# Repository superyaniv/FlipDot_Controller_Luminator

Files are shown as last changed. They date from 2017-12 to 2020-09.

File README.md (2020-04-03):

# FlipDot Controller Project

A FlipDot board was a unique way, before the cheap and ubiquitous LED displays, to display signage with low power and high visability. The unique innovation combines electrical engineering princples of electromagnetism, polarity, multiplexing, and much more. Not to mention it's just fun to see the complex mechanical switching in realtime. As I became interested in learning more about electrical engineering and design, this project, created in 2011 and posted on my public git recently, inspired me to begin learning circuit design. 

## Getting Started

The PCB schemetic uses 10 shift registers to drive darlington array source and pull down ICs. The pin layout is explained in the cvs file. From there, the project uses the flipdot controller python class to post bytes to the board and pin layout. The layer of abstraction above that can be a variance of code, depending on what to pull and post to the board. Examples included here are a clock, bitcoin price feed, and twitter display.

### Prerequisites

Hardware necessary to complete the code from scratch include:

```
10 x 595 Shift Registers
5 x ULN2803 Darlington Arrays
5 x Source Drivers (x2981)
Note: A different layout could use MOSFET transistors instead of these ICs.

1 x microcontroller (RPI or ESP8266 for use with this python code or Arduino )
```

### View of the PCB

Top, Bottom, and overall Design View of the PCB:

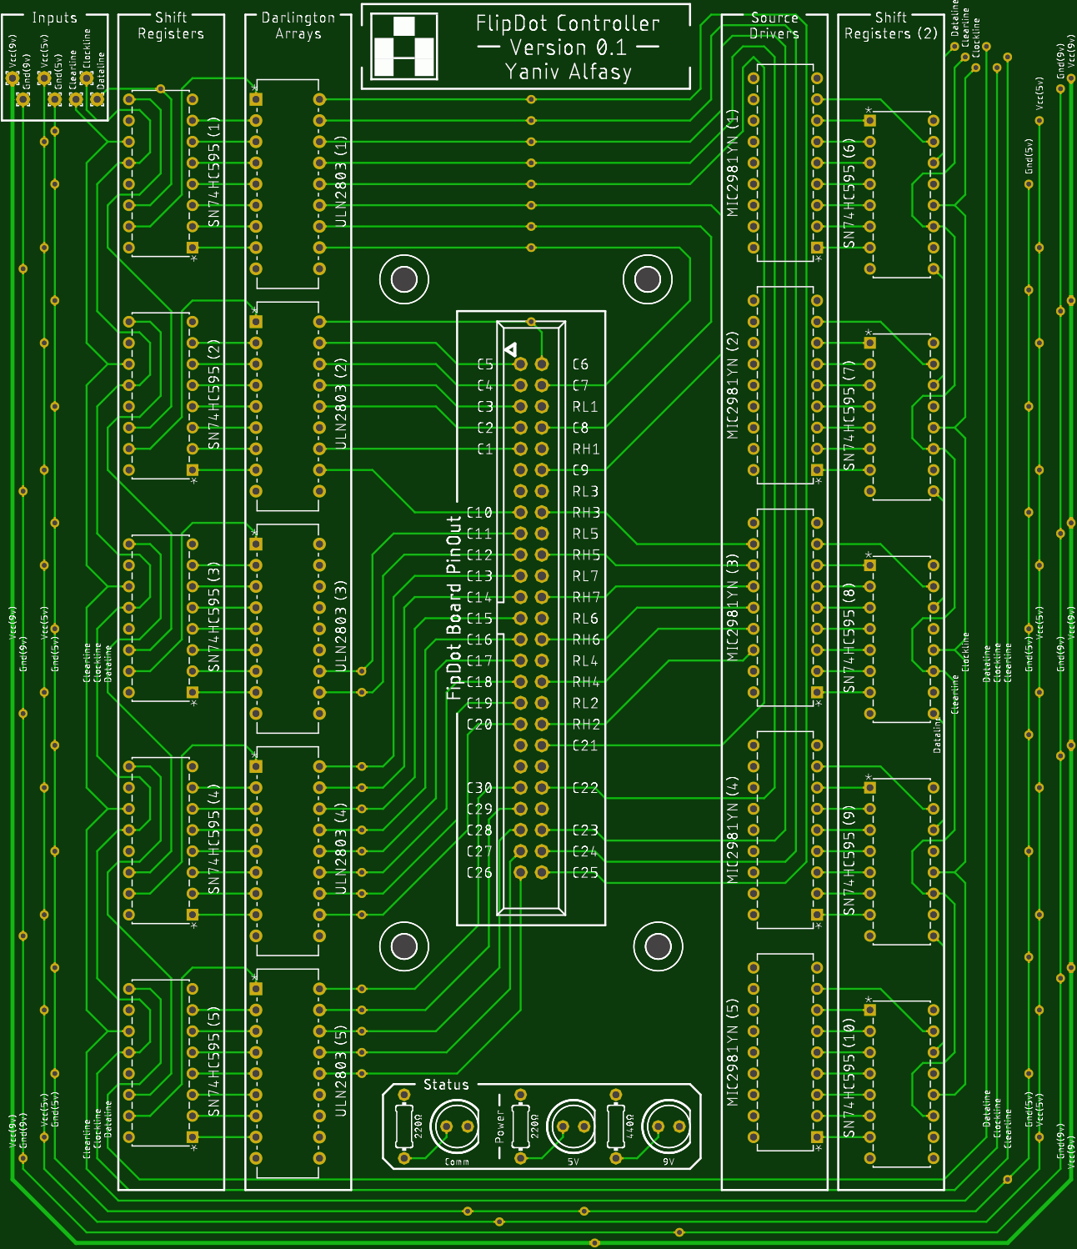
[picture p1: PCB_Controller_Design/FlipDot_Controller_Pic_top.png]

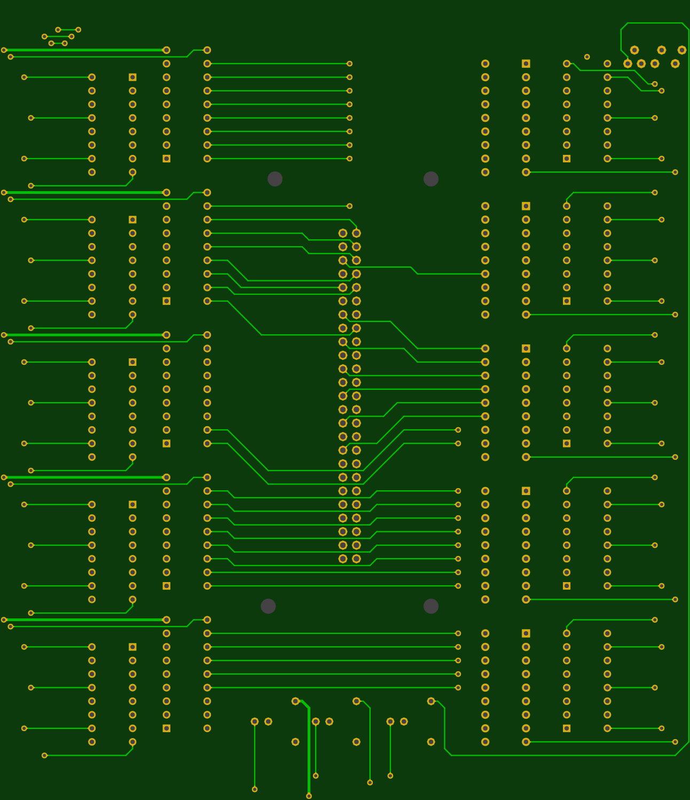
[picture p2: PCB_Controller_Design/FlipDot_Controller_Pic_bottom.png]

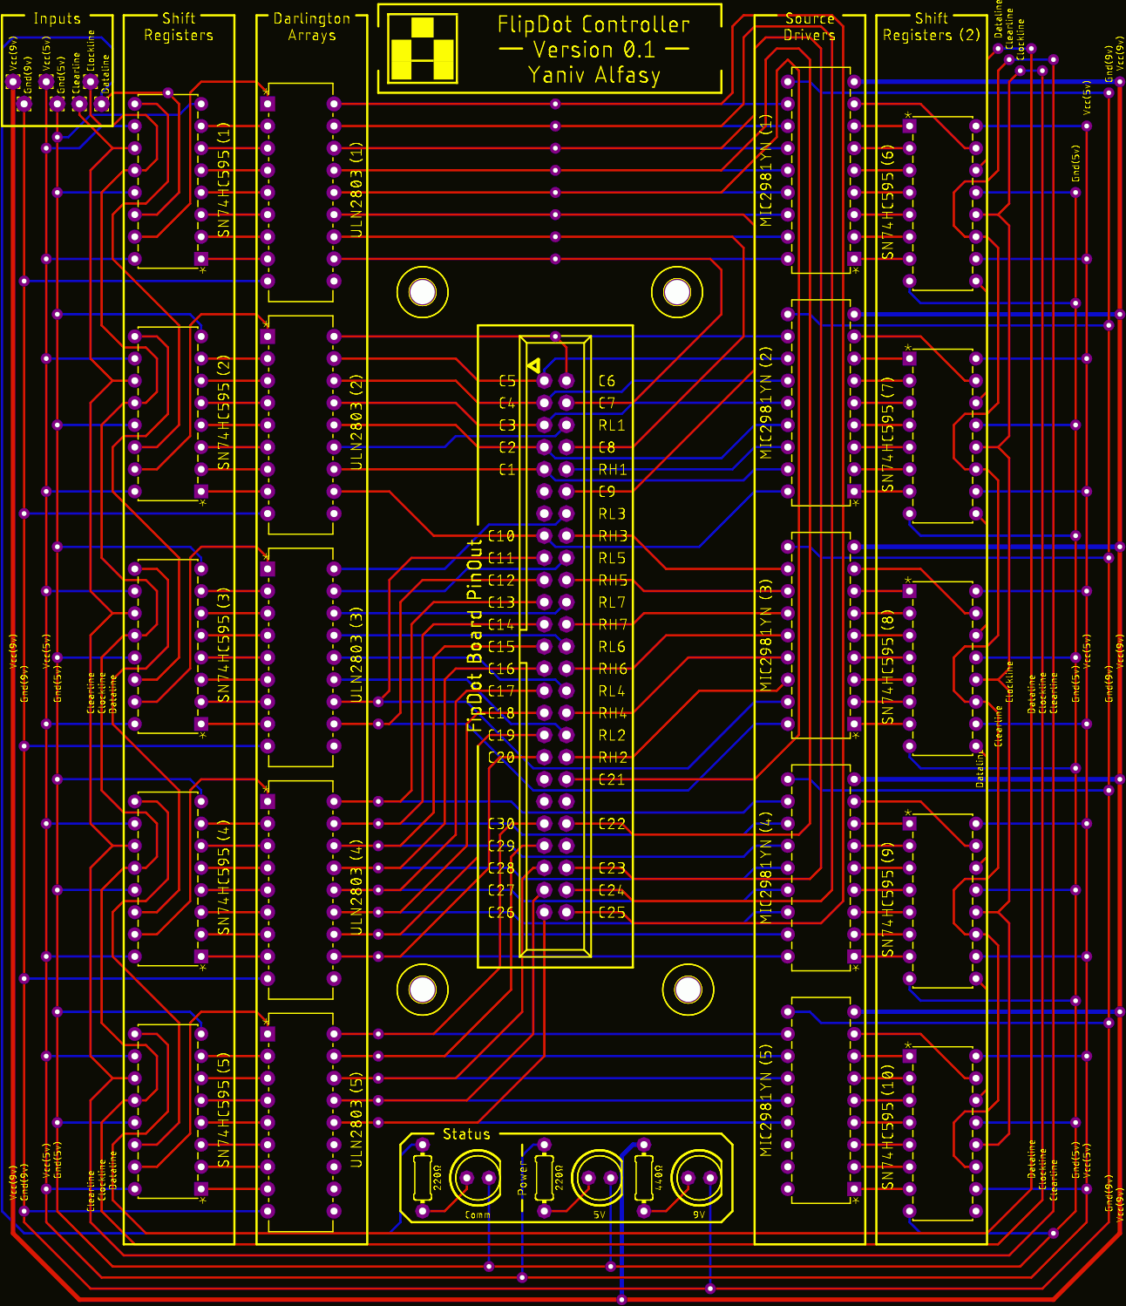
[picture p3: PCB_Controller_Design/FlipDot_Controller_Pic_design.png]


### Installing

Using the gerber files, you can have the board made at a host of pcb manufacturers. Alternatively you can design the board yourself with a breadboard.

Set up the layout of the board:

```
Using the gerber files, you can have the board made at a host of pcb manufacturers. 

Alternatively you can design the board yourself with a breadboard.
```

Wire your board:

```
Wire the board according to the schematic.

Connect the board to the flip-dot display and the microcontroller.
(use pins 18, 23, and 24 for the shift register data, clock, clear)
```

Connect to Power:

```
Connect the board to power, 9V for to drive the dots, and 5V to the registers.
```

End with an example of getting some data out of the system or using it for a little demo

## Running the tests

Run tests to the shift registers first, to ensure the correct outputs from the registers.

Run tests to the source and pull drivers, to ensure the 9V supply is being triggered to the dots.

Use the attached LEDs to check power to the board.

If you are using APIs to get input for the display, check the output of those APIs by uncommenting the debug and print lines.

## Deployment

Add additional notes about how to deploy this on a live system

## Authors

Yaniv Joseph Alfasy (https://yanivalfasy.com)

Please contact me if you have any additional questions.

## License

No licensing decided yet.

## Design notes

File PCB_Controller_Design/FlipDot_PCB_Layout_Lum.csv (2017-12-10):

Shift Register Count | Socket Pin | Row/column | Row/Column | Flip
10 | 9 | 1 | Column | Off
12 | 7 | 2 | Column | Off
13 | 5 | 3 | Column | Off
14 | 3 | 4 | Column | Off
15 | 1 | 5 | Column | Off
8 | 2 | 6 | Column | Off
1 | 4 | 7 | Column | Off
2 | 8 | 8 | Column | Off
3 | 12 | 9 | Column | Off
9 | 15 | 10 | Column | Off
18 | 17 | 11 | Column | Off
17 | 19 | 12 | Column | Off
24 | 21 | 13 | Column | Off
31 | 23 | 14 | Column | Off
30 | 25 | 15 | Column | Off
29 | 27 | 16 | Column | Off
28 | 29 | 17 | Column | Off
27 | 31 | 18 | Column | Off
26 | 33 | 19 | Column | Off
25 | 35 | 20 | Column | Off
4 | 38 | 21 | Column | Off
5 | 42 | 22 | Column | Off
6 | 46 | 23 | Column | Off
7 | 48 | 24 | Column | Off
0 | 50 | 25 | Column | Off
36 | 49 | 26 | Column | Off
37 | 47 | 27 | Column | Off
38 | 45 | 28 | Column | Off
39 | 43 | 29 | Column | Off
32 | 41 | 30 | Column | Off
11 | 6 | 1 | Row | Off
19 | 34 | 2 | Row | Off
16 | 14 | 3 | Row | Off
20 | 30 | 4 | Row | Off
23 | 18 | 5 | Row | Off
21 | 26 | 6 | Row | Off
22 | 22 | 7 | Row | Off
54 | 9 | 1 | Column | On
52 | 7 | 2 | Column | On
51 | 5 | 3 | Column | On
50 | 3 | 4 | Column | On
49 | 1 | 5 | Column | On
48 | 2 | 6 | Column | On
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

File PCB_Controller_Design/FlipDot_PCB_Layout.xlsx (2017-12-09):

Shift Register Count | Pin | Row/column | Row/Column | Flip
10 | 30 | 1 | Column | Off | Off Columns | [10,12,13,14,15,8,1,2,3,9,18,17,24,31,30,29,28,27,26,25,4,5,6,7,0,36,37,38,39,32]
12 | 29 | 2 | Column | Off | On Columns | [54,52,51,50,49,48,47,46,45,55,62,63,64,65,66,67,68,69,70,71,44,43,42,41,40,76,75,74,73,72]
13 | 28 | 3 | Column | Off | Off Rows | [11,19,16,20,23,21,22]
14 | 27 | 4 | Column | Off | On Rows | [53,61,56,60,57,59,58]
15 | 26 | 5 | Column | Off
8 | 1 | 6 | Column | Off
1 | 2 | 7 | Column | Off
2 | 4 | 8 | Column | Off
3 | 6 | 9 | Column | Off
9 | 33 | 10 | Column | Off
18 | 34 | 11 | Column | Off
17 | 35 | 12 | Column | Off
24 | 36 | 13 | Column | Off
31 | 37 | 14 | Column | Off
30 | 38 | 15 | Column | Off
29 | 39 | 16 | Column | Off
28 | 40 | 17 | Column | Off
27 | 41 | 18 | Column | Off
26 | 42 | 19 | Column | Off
25 | 43 | 20 | Column | Off
4 | 19 | 21 | Column | Off
5 | 21 | 22 | Column | Off
6 | 23 | 23 | Column | Off
7 | 24 | 24 | Column | Off
0 | 25 | 25 | Column | Off
36 | 50 | 26 | Column | Off
37 | 49 | 27 | Column | Off
38 | 48 | 28 | Column | Off
39 | 47 | 29 | Column | Off
32 | 46 | 30 | Column | Off
11 | 3 | 1 | Row | Off
19 | 17 | 2 | Row | Off
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

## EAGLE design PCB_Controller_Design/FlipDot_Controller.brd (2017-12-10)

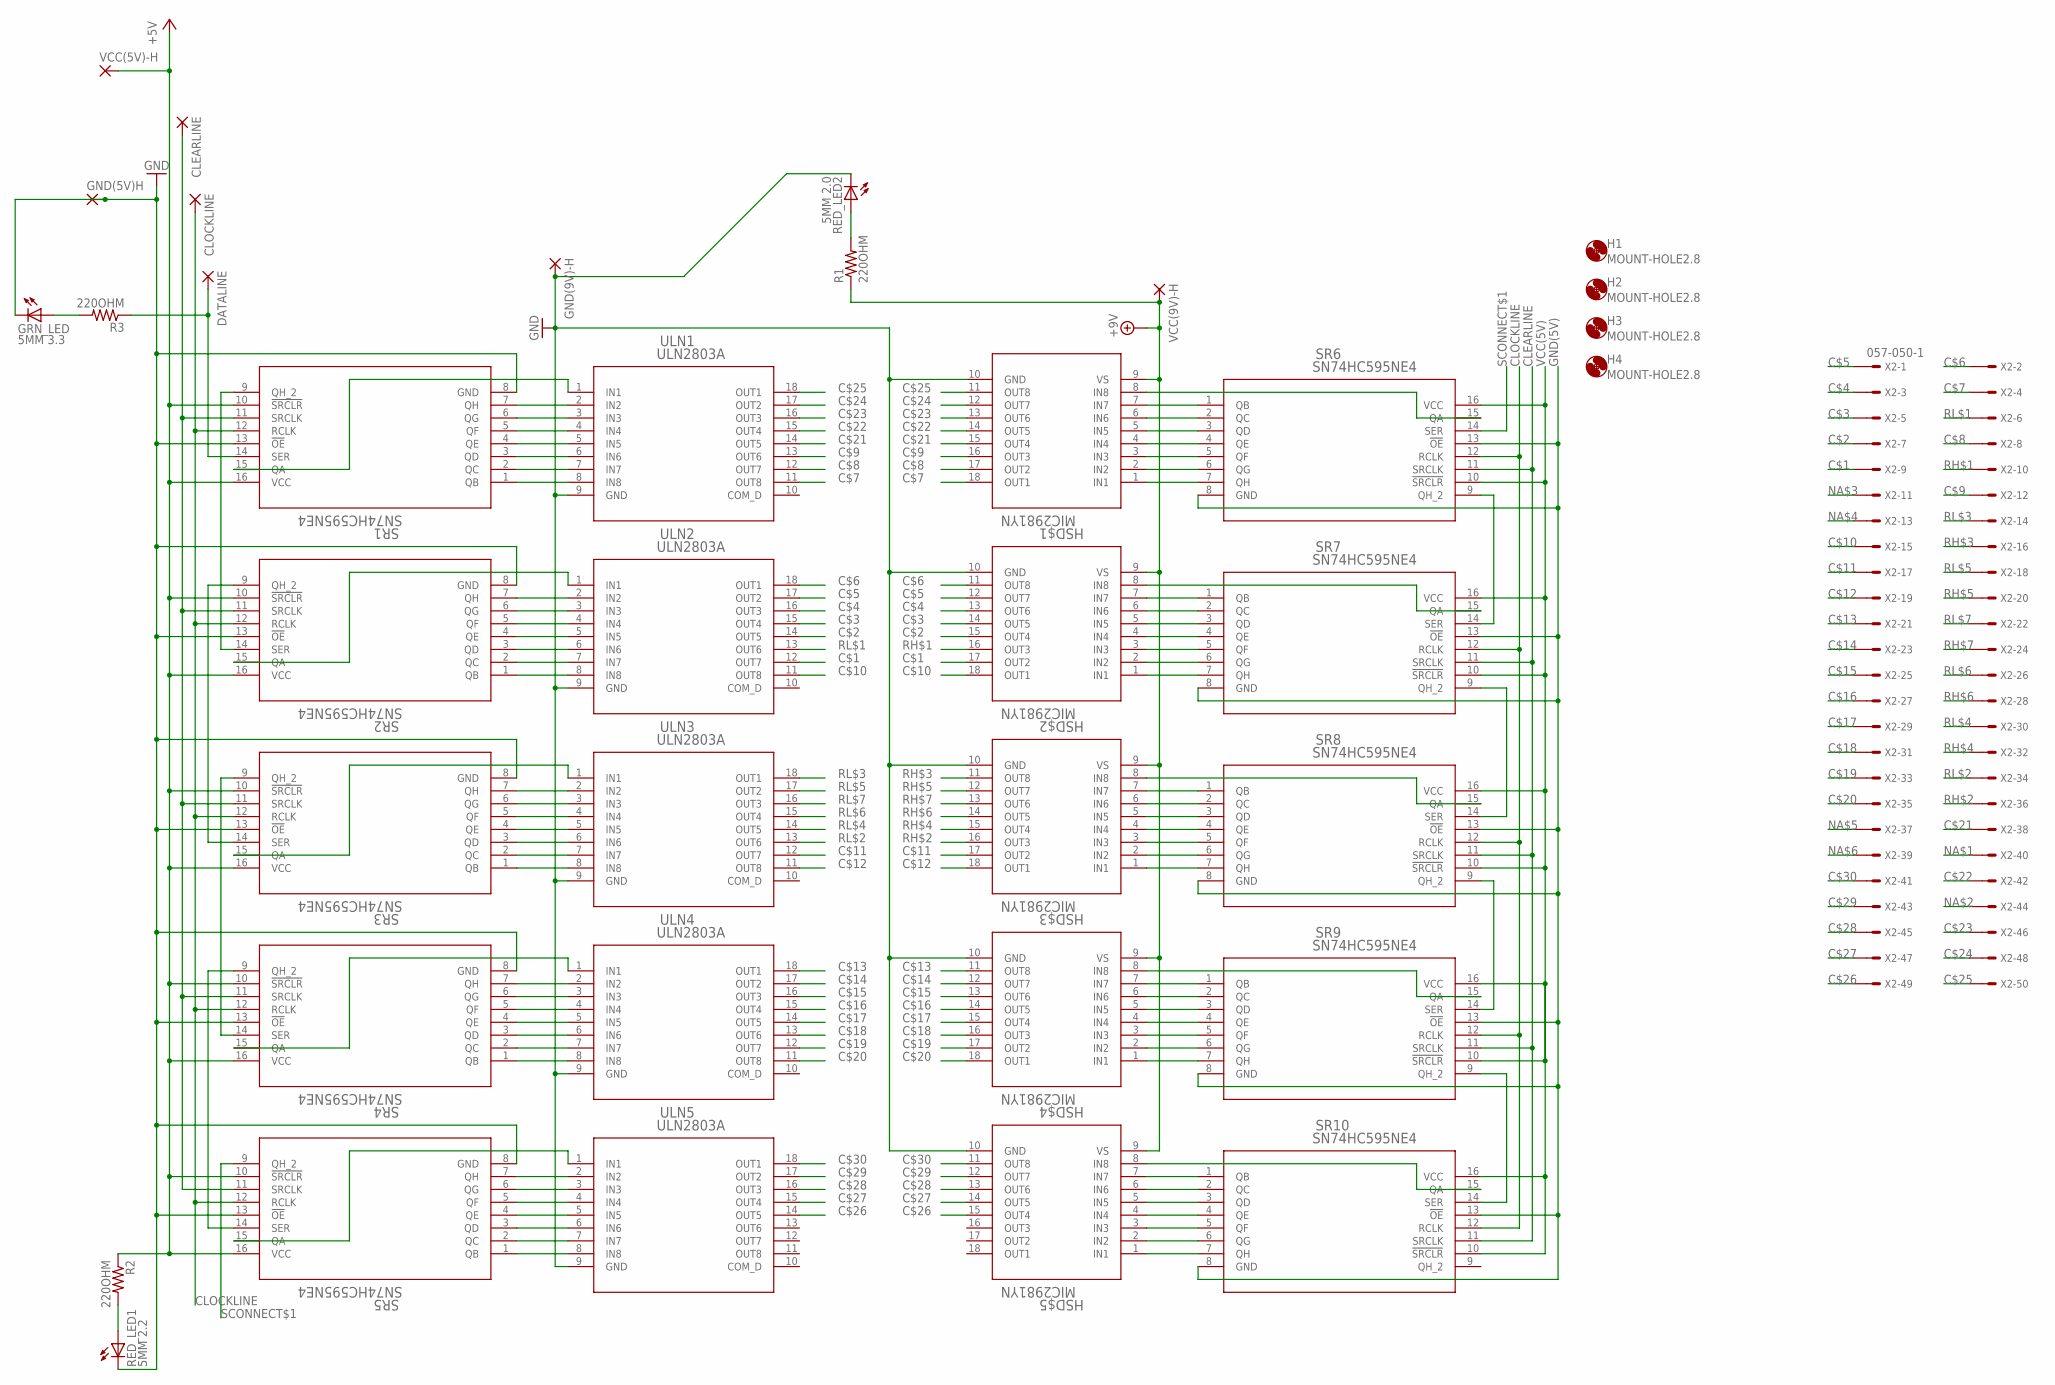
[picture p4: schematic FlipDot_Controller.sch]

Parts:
CLEARLINE: WIREPAD1,6/0,8; 1,6/0,8
CLOCKLINE: WIREPAD1,6/0,8; 1,6/0,8
DATALINE: WIREPAD1,6/0,8; 1,6/0,8
GND(5V)H, GND(9V)-H: WIREPAD1,6/0,8; 1,6/0,8
GRN_LED: 5MM 3.3; LED5MM
H1, H2, H3, H4: MOUNT-HOLE2.8; 2,8
HSD$1, HSD$2, HSD$3, HSD$4, HSD$5: MIC2981YN; PDIP-18
R1, R2, R3: 220OHM; 0204/7
RED_LED1: 5MM 2.2; LED5MM
RED_LED2: 5MM 2.0; LED5MM
SR1, SR2, SR3, SR4, SR5, SR6, SR7, SR8, SR9, SR10: SN74HC595NE4; N16
ULN1, ULN2, ULN3, ULN4, ULN5: ULN2803A; DIP-18
VCC(5V)-H, VCC(9V)-H: WIREPAD1,6/0,8; 1,6/0,8
X2: 057-050-1

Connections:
+9V: HSD$1.9 (VS), HSD$2.9 (VS), HSD$3.9 (VS), HSD$4.9 (VS), HSD$5.9 (VS), R1.1, VCC(9V)-H.1
C$1: HSD$2.17 (OUT2), ULN2.12 (OUT7), X2.9
C$2: HSD$2.15 (OUT4), ULN2.14 (OUT5), X2.7
C$3: HSD$2.14 (OUT5), ULN2.15 (OUT4), X2.5
C$4: HSD$2.13 (OUT6), ULN2.16 (OUT3), X2.3
C$5: HSD$2.12 (OUT7), ULN2.17 (OUT2), X2.1
C$6: HSD$2.11 (OUT8), ULN2.18 (OUT1), X2.2
C$7: HSD$1.18 (OUT1), ULN1.11 (OUT8), X2.4
C$8: HSD$1.17 (OUT2), ULN1.12 (OUT7), X2.8
C$9: HSD$1.16 (OUT3), ULN1.13 (OUT6), X2.12
C$10: HSD$2.18 (OUT1), ULN2.11 (OUT8), X2.15
C$11: HSD$3.17 (OUT2), ULN3.12 (OUT7), X2.17
C$12: HSD$3.18 (OUT1), ULN3.11 (OUT8), X2.19
C$13: HSD$4.11 (OUT8), ULN4.18 (OUT1), X2.21
C$14: HSD$4.12 (OUT7), ULN4.17 (OUT2), X2.23
C$15: HSD$4.13 (OUT6), ULN4.16 (OUT3), X2.25
C$16: HSD$4.14 (OUT5), ULN4.15 (OUT4), X2.27
C$17: HSD$4.15 (OUT4), ULN4.14 (OUT5), X2.29
C$18: HSD$4.16 (OUT3), ULN4.13 (OUT6), X2.31
C$19: HSD$4.17 (OUT2), ULN4.12 (OUT7), X2.33
C$20: HSD$4.18 (OUT1), ULN4.11 (OUT8), X2.35
C$21: HSD$1.15 (OUT4), ULN1.14 (OUT5), X2.38
C$22: HSD$1.14 (OUT5), ULN1.15 (OUT4), X2.42
C$23: HSD$1.13 (OUT6), ULN1.16 (OUT3), X2.46
C$24: HSD$1.12 (OUT7), ULN1.17 (OUT2), X2.48
C$25: HSD$1.11 (OUT8), ULN1.18 (OUT1), X2.50
C$26: HSD$5.15 (OUT4), ULN5.14 (OUT5), X2.49
C$27: HSD$5.14 (OUT5), ULN5.15 (OUT4), X2.47
C$28: HSD$5.13 (OUT6), ULN5.16 (OUT3), X2.45
C$29: HSD$5.12 (OUT7), ULN5.17 (OUT2), X2.43
C$30: HSD$5.11 (OUT8), ULN5.18 (OUT1), X2.41
CLEARLINE: CLEARLINE.1, SR1.11 (SRCLK), SR2.11 (SRCLK), SR3.11 (SRCLK), SR4.11 (SRCLK), SR5.11 (SRCLK), SR6.11 (SRCLK), SR7.11 (SRCLK), SR8.11 (SRCLK), SR9.11 (SRCLK), SR10.11 (SRCLK)
CLOCKLINE: CLOCKLINE.1, SR1.12 (RCLK), SR2.12 (RCLK), SR3.12 (RCLK), SR4.12 (RCLK), SR5.12 (RCLK), SR6.12 (RCLK), SR7.12 (RCLK), SR8.12 (RCLK), SR9.12 (RCLK), SR10.12 (RCLK)
DATALINE: DATALINE.1, R3.1, SR1.14 (SER)
GND(5V): GND(5V)H.1, GRN_LED.K (C), RED_LED1.K (C), SR1.8 (GND), SR1.13 (!OE), SR2.8 (GND), SR2.13 (!OE), SR3.8 (GND), SR3.13 (!OE), SR4.8 (GND), SR4.13 (!OE), SR5.8 (GND), SR5.13 (!OE), SR6.8 (GND), SR6.13 (!OE), SR7.8 (GND), SR7.13 (!OE), SR8.8 (GND), SR8.13 (!OE), SR9.8 (GND), SR9.13 (!OE), SR10.8 (GND), SR10.13 (!OE)
GND(9V): GND(9V)-H.1, HSD$1.10 (GND), HSD$2.10 (GND), HSD$3.10 (GND), HSD$4.10 (GND), HSD$5.10 (GND), RED_LED2.K (C), ULN1.9 (GND), ULN2.9 (GND), ULN3.9 (GND), ULN4.9 (GND), ULN5.9 (GND)
unnamed: SR1.15 (QA), ULN1.1 (IN1)
unnamed: SR1.1 (QB), ULN1.8 (IN8)
unnamed: SR1.2 (QC), ULN1.7 (IN7)
unnamed: SR1.3 (QD), ULN1.6 (IN6)
unnamed: SR1.4 (QE), ULN1.5 (IN5)
unnamed: SR1.5 (QF), ULN1.4 (IN4)
unnamed: SR1.6 (QG), ULN1.3 (IN3)
unnamed: SR1.9 (QH_2), SR2.14 (SER)
unnamed: SR1.7 (QH), ULN1.2 (IN2)
unnamed: SR6.9 (QH_2), SR7.14 (SER)
unnamed: SR7.9 (QH_2), SR8.14 (SER)
unnamed: SR8.9 (QH_2), SR9.14 (SER)
unnamed: SR2.15 (QA), ULN2.1 (IN1)
unnamed: SR2.9 (QH_2), SR3.14 (SER)
unnamed: SR4.15 (QA), ULN4.1 (IN1)
unnamed: SR2.7 (QH), ULN2.2 (IN2)
unnamed: SR2.6 (QG), ULN2.3 (IN3)
unnamed: SR2.5 (QF), ULN2.4 (IN4)
unnamed: SR2.4 (QE), ULN2.5 (IN5)
unnamed: SR2.3 (QD), ULN2.6 (IN6)
unnamed: SR2.2 (QC), ULN2.7 (IN7)
unnamed: SR3.15 (QA), ULN3.1 (IN1)
unnamed: SR3.9 (QH_2), SR4.14 (SER)
unnamed: SR4.9 (QH_2), SR5.14 (SER)
unnamed: SR5.15 (QA), ULN5.1 (IN1)
unnamed: SR4.7 (QH), ULN4.2 (IN2)
unnamed: SR3.7 (QH), ULN3.2 (IN2)
unnamed: SR3.6 (QG), ULN3.3 (IN3)
unnamed: SR3.5 (QF), ULN3.4 (IN4)
unnamed: SR3.4 (QE), ULN3.5 (IN5)
unnamed: SR3.3 (QD), ULN3.6 (IN6)
unnamed: SR3.2 (QC), ULN3.7 (IN7)
unnamed: HSD$1.8 (IN8), SR6.15 (QA)
unnamed: SR5.7 (QH), ULN5.2 (IN2)
unnamed: HSD$1.7 (IN7), SR6.1 (QB)
unnamed: HSD$1.6 (IN6), SR6.2 (QC)
unnamed: SR4.6 (QG), ULN4.3 (IN3)
unnamed: SR4.5 (QF), ULN4.4 (IN4)
unnamed: SR4.4 (QE), ULN4.5 (IN5)
unnamed: SR4.3 (QD), ULN4.6 (IN6)
unnamed: SR4.2 (QC), ULN4.7 (IN7)
unnamed: SR4.1 (QB), ULN4.8 (IN8)
unnamed: SR5.6 (QG), ULN5.3 (IN3)
unnamed: HSD$1.5 (IN5), SR6.3 (QD)
unnamed: HSD$1.4 (IN4), SR6.4 (QE)
unnamed: SR5.5 (QF), ULN5.4 (IN4)
unnamed: SR5.4 (QE), ULN5.5 (IN5)
unnamed: SR5.3 (QD), ULN5.6 (IN6)
unnamed: SR5.2 (QC), ULN5.7 (IN7)
unnamed: SR5.1 (QB), ULN5.8 (IN8)
unnamed: HSD$1.3 (IN3), SR6.5 (QF)
unnamed: HSD$1.2 (IN2), SR6.6 (QG)
unnamed: HSD$1.1 (IN1), SR6.7 (QH)
unnamed: SR9.9 (QH_2), SR10.14 (SER)
unnamed: HSD$2.8 (IN8), SR7.15 (QA)
unnamed: HSD$3.8 (IN8), SR8.15 (QA)
unnamed: HSD$4.8 (IN8), SR9.15 (QA)
unnamed: HSD$5.8 (IN8), SR10.15 (QA)
unnamed: HSD$2.7 (IN7), SR7.1 (QB)
unnamed: HSD$2.6 (IN6), SR7.2 (QC)
unnamed: HSD$2.5 (IN5), SR7.3 (QD)
unnamed: HSD$2.4 (IN4), SR7.4 (QE)
unnamed: HSD$2.3 (IN3), SR7.5 (QF)
unnamed: HSD$2.2 (IN2), SR7.6 (QG)
unnamed: HSD$2.1 (IN1), SR7.7 (QH)
unnamed: HSD$3.7 (IN7), SR8.1 (QB)
unnamed: HSD$3.6 (IN6), SR8.2 (QC)
unnamed: HSD$3.5 (IN5), SR8.3 (QD)
unnamed: HSD$3.4 (IN4), SR8.4 (QE)
unnamed: HSD$3.3 (IN3), SR8.5 (QF)
unnamed: HSD$3.2 (IN2), SR8.6 (QG)
unnamed: HSD$3.1 (IN1), SR8.7 (QH)
unnamed: HSD$4.7 (IN7), SR9.1 (QB)
unnamed: HSD$4.6 (IN6), SR9.2 (QC)
unnamed: HSD$4.5 (IN5), SR9.3 (QD)
unnamed: HSD$4.4 (IN4), SR9.4 (QE)
unnamed: HSD$4.3 (IN3), SR9.5 (QF)
unnamed: HSD$4.2 (IN2), SR9.6 (QG)
unnamed: HSD$4.1 (IN1), SR9.7 (QH)
unnamed: HSD$5.7 (IN7), SR10.1 (QB)
unnamed: HSD$5.6 (IN6), SR10.2 (QC)
unnamed: HSD$5.5 (IN5), SR10.3 (QD)
unnamed: HSD$5.4 (IN4), SR10.4 (QE)
unnamed: HSD$5.3 (IN3), SR10.5 (QF)
unnamed: HSD$5.2 (IN2), SR10.6 (QG)
unnamed: HSD$5.1 (IN1), SR10.7 (QH)
unnamed: SR2.1 (QB), ULN2.8 (IN8)
unnamed: SR3.1 (QB), ULN3.8 (IN8)
unnamed: R2.2, RED_LED1.A
unnamed: R1.2, RED_LED2.A
unnamed: GRN_LED.A, R3.2
NA$1: X2.40
NA$2: X2.44
NA$3: X2.11
NA$4: X2.13
NA$5: X2.37
NA$6: X2.39
RH$1: HSD$2.16 (OUT3), X2.10
RH$2: HSD$3.16 (OUT3), X2.36
RH$3: HSD$3.11 (OUT8), X2.16
RH$4: HSD$3.15 (OUT4), X2.32
RH$5: HSD$3.12 (OUT7), X2.20
RH$6: HSD$3.14 (OUT5), X2.28
RH$7: HSD$3.13 (OUT6), X2.24
RL$1: ULN2.13 (OUT6), X2.6
RL$2: ULN3.13 (OUT6), X2.34
RL$3: ULN3.18 (OUT1), X2.14
RL$4: ULN3.14 (OUT5), X2.30
RL$5: ULN3.17 (OUT2), X2.18
RL$6: ULN3.15 (OUT4), X2.26
RL$7: ULN3.16 (OUT3), X2.22
SCONNECT$1: SR5.9 (QH_2), SR6.14 (SER)
VCC(5V): R2.1, SR1.10 (!SRCLR), SR1.16 (VCC), SR2.10 (!SRCLR), SR2.16 (VCC), SR3.10 (!SRCLR), SR3.16 (VCC), SR4.10 (!SRCLR), SR4.16 (VCC), SR5.10 (!SRCLR), SR5.16 (VCC), SR6.10 (!SRCLR), SR6.16 (VCC), SR7.10 (!SRCLR), SR7.16 (VCC), SR8.10 (!SRCLR), SR8.16 (VCC), SR9.10 (!SRCLR), SR9.16 (VCC), SR10.10 (!SRCLR), SR10.16 (VCC), VCC(5V)-H.1

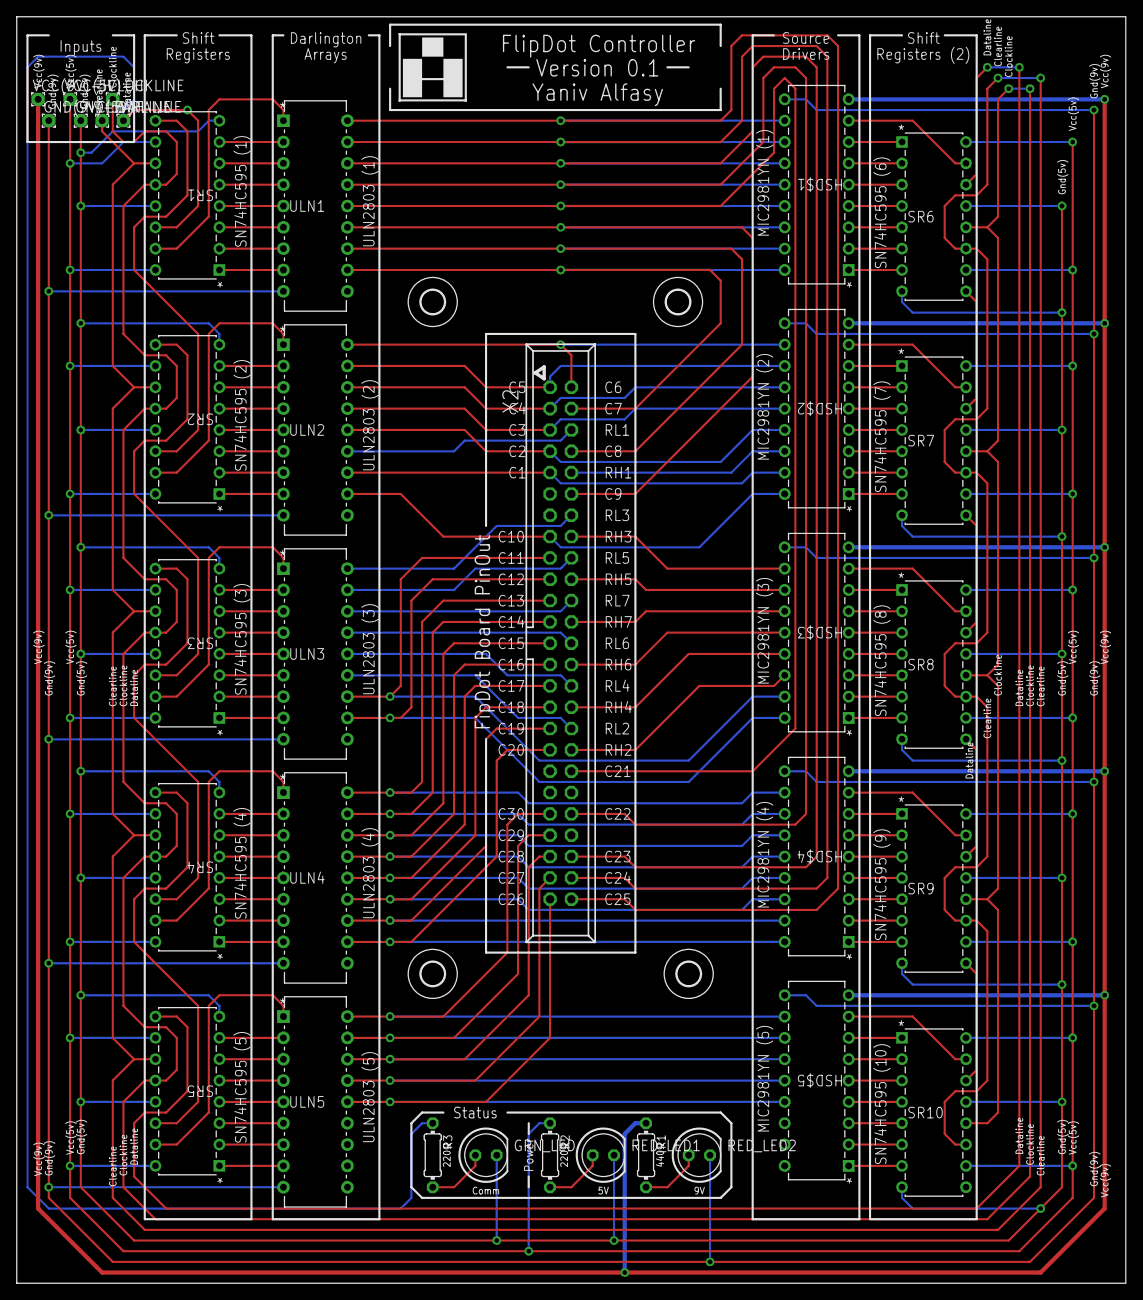
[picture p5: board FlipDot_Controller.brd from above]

Board: 2 copper layers, 132.1 x 150.8 mm, 38 parts (0 on the bottom side), 143 nets.

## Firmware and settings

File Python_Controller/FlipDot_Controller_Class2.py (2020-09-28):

import RPi.GPIO as IO
from time import sleep

class FlipDot_Controller_Class:

    alphabet = [[0x00,0x00,0x00,0x00,0x00],[0x00,0x00,0x6f,0x00,0x00],[0x00,0x07,0x00,0x07,0x00],[0x14,0x7f,0x14,0x7f,0x14],[0x00,0x07,0x04,0x1e,0x00],[0x23,0x13,0x08,0x64,0x62],[0x36,0x49,0x56,0x20,0x50],[0x00,0x00,0x07,0x00,0x00],[0x00,0x1c,0x22,0x41,0x00],[0x00,0x41,0x22,0x1c,0x00],[0x14,0x08,0x3e,0x08,0x14],[0x08,0x08,0x3e,0x08,0x08],[0x00,0x50,0x30,0x00,0x00],[0x08,0x08,0x08,0x08,0x08],[0x00,0x60,0x60,0x00,0x00],[0x20,0x10,0x08,0x04,0x02],[0x3e,0x51,0x49,0x45,0x3e],[0x00,0x42,0x7f,0x40,0x00],[0x42,0x61,0x51,0x49,0x46],[0x21,0x41,0x45,0x4b,0x31],[0x18,0x14,0x12,0x7f,0x10],[0x27,0x45,0x45,0x45,0x39],[0x3c,0x4a,0x49,0x49,0x30],[0x01,0x71,0x09,0x05,0x03],[0x36,0x49,0x49,0x49,0x36],[0x06,0x49,0x49,0x29,0x1e],[0x00,0x36,0x36,0x00,0x00],[0x00,0x56,0x36,0x00,0x00],[0x08,0x14,0x22,0x41,0x00],[0x14,0x14,0x14,0x14,0x14],[0x00,0x41,0x22,0x14,0x08],[0x02,0x01,0x51,0x09,0x06],[0x3e,0x41,0x5d,0x49,0x4e],[0x7e,0x09,0x09,0x09,0x7e],[0x7f,0x49,0x49,0x49,0x36],[0x3e,0x41,0x41,0x41,0x22],[0x7f,0x41,0x41,0x41,0x3e],[0x7f,0x49,0x49,0x49,0x41],[0x7f,0x09,0x09,0x09,0x01],[0x3e,0x41,0x49,0x49,0x7a],[0x7f,0x08,0x08,0x08,0x7f],[0x00,0x41,0x7f,0x41,0x00],[0x20,0x40,0x41,0x3f,0x01],[0x7f,0x08,0x14,0x22,0x41],[0x7f,0x40,0x40,0x40,0x40],[0x7f,0x02,0x0c,0x02,0x7f],[0x7f,0x04,0x08,0x10,0x7f],[0x3e,0x41,0x41,0x41,0x3e],[0x7f,0x09,0x09,0x09,0x06],[0x3e,0x41,0x51,0x21,0x5e],[0x7f,0x09,0x19,0x29,0x46],[0x46,0x49,0x49,0x49,0x31],[0x01,0x01,0x7f,0x01,0x01],[0x3f,0x40,0x40,0x40,0x3f],[0x0f,0x30,0x40,0x30,0x0f],[0x3f,0x40,0x30,0x40,0x3f],[0x63,0x14,0x08,0x14,0x63],[0x07,0x08,0x70,0x08,0x07],[0x61,0x51,0x49,0x45,0x43],[0x3c,0x4a,0x49,0x29,0x1e],[0x02,0x04,0x08,0x10,0x20],[0x00,0x41,0x7f,0x00,0x00],[0x04,0x02,0x01,0x02,0x04],[0x40,0x40,0x40,0x40,0x40],[0x00,0x00,0x03,0x04,0x00],[0x20,0x54,0x54,0x54,0x78],[0x7f,0x48,0x44,0x44,0x38],[0x38,0x44,0x44,0x44,0x20],[0x38,0x44,0x44,0x48,0x7f],[0x38,0x54,0x54,0x54,0x18],[0x08,0x7e,0x09,0x01,0x02],[0x0c,0x52,0x52,0x52,0x3e],[0x7f,0x08,0x04,0x04,0x78],[0x00,0x44,0x7d,0x40,0x00],[0x20,0x40,0x44,0x3d,0x00],[0x00,0x7f,0x10,0x28,0x44],[0x00,0x41,0x7f,0x40,0x00],[0x7c,0x04,0x18,0x04,0x78],[0x7c,0x08,0x04,0x04,0x78],[0x38,0x44,0x44,0x44,0x38],[0x7c,0x14,0x14,0x14,0x08],[0x08,0x14,0x14,0x18,0x7c],[0x7c,0x08,0x04,0x04,0x08],[0x48,0x54,0x54,0x54,0x20],[0x04,0x3f,0x44,0x40,0x20],[0x3c,0x40,0x40,0x20,0x7c],[0x1c,0x20,0x40,0x20,0x1c],[0x3c,0x40,0x30,0x40,0x3c],[0x44,0x28,0x10,0x28,0x44],[0x0c,0x50,0x50,0x50,0x3c],[0x44,0x64,0x54,0x4c,0x44],[0x00,0x08,0x36,0x41,0x41],[0x00,0x00,0x7f,0x00,0x00],[0x41,0x41,0x36,0x08,0x00],[0x04,0x02,0x04,0x08,0x04]]
    columns_per_Segment = 5
    displayColumns = 25
    displayRows = 7

    def __init__(self, name, onRows, offRows, onColumns, offColumns, numOfRegisterPins, ser_Pin, rclk_Pin, srclk_Pin):
        self.name = name    # Name of the controller or panel
        self.onRows = onRows    # OnRow pins
        self.offRows = offRows
        self.onColumns = onColumns
        self.offColumns = offColumns
        self.numOfRegisterPins = numOfRegisterPins
        self.ser_Pin = ser_Pin
        self.rclk_Pin = rclk_Pin
        self.srclk_Pin = srclk_Pin
        self.initializePI()
        self.registers= [0] * numOfRegisterPins
        self.oldDisplayState = [[0 for s in range(self.displayRows)] for c in range(self.displayColumns)]
        self.flipDelay = .015 #timing1

    def initializePI(self):
        IO.setmode(IO.BCM)
        IO.setup(self.ser_Pin,IO.OUT)
        IO.setup(self.rclk_Pin,IO.OUT)
        IO.setup(self.srclk_Pin,IO.OUT)

    def choose_Alphabet(self, newAlphabet):
        self.alphabet = newAlphabet
        #Alphabet = [[0,0,0,0,0],[0,56,125,56,0],[80,96,0,80,96],[20,127,20,127,20],[18,42,127,42,36],[98,100,8,19,35],[54,73,85,34,5],[0,80,96,0,0], [0,28,34,65,0],[0,65,34,28,0],[20,8,62,8,20],[8,8,62,8,8],[0,5,6,0,0],[8,8,8,8,8],[0,3,3,0,0],[2,4,8,16,32],[62,69,73,81,62],[17,33,127,1,1],[33,67,69,73,49],[34,65,73,73,54],[12,20,36,127,4],[114,81,81,81,78],[62,73,73,73,38],[64,71,72,80,96],[54,73,73,73,54],[50,73,73,73,62],[0,54,54,0,0],[0,53,54,0,0],[8,20,34,65,0],[20,20,20,20,20],[0,65,34,20,8],[32,64,69,72,48],[62,73,87,85,62],[31, 36, 68, 36, 31],[127, 73, 73, 73, 54],[62, 65, 65, 65, 34],[127, 65, 65, 34, 28],[127, 73, 73, 65, 65],[127, 72, 72, 72, 64],[62, 65, 65, 69, 38],[127, 8, 8, 8, 127],[0, 65, 127, 65, 0],[2, 1, 1, 1, 126],[127, 8, 20, 34, 65],[127, 1, 1, 1, 1],[127, 32, 16, 32, 127],[127, 32, 16, 8, 127],[62, 65, 65, 65, 62],[127, 72, 72, 72, 48],[62, 65, 69, 66, 61],[127, 72, 76, 74, 49],[50, 73, 73, 73, 38],[64, 64, 127, 64, 64],[126, 1, 1, 1, 126],[124, 2, 1, 2, 124],[126, 1, 6, 1, 126],[99, 20, 8, 20, 99],[96, 16, 15, 16, 96],[67, 69, 73, 81, 97],[0,127,65,65,0],[32,16,8,4,2],[0,65,65,127,0],[16,32,64,32,16],[1,1,1,1,1],[0,64,32,16,0],[2,21,21,14,1],[64,126,9,17,14],[14,17,17,17,10],[14,17,74,127,1],[14,21,21,21,9],[1,9,63,72,32],[9,21,21,21,30],[127,8,8,8,7],[0,0,46,1,1],[2,1,1,1,94],[1,127,4,10,17],[0,65,127,1,0],[31,16,14,16,31],[31,8,16,16,15],[14,17,17,17,14],[127,20,20,20,8],[8,20,20,31,1],[31,8,16,16,8],[9,21,21,21,18],[16,16,126,17,18],[30,1,1,30,1],[28,2,1,2,28],[30,1,6,1,30],[17,10,4,10,17],[16,9,6,8,16],[17,19,21,25,17],[8,54,65,65,0],[0,0,127,0,0],[0,65,65,54,8],[32,64,32,16,32]]

    def writeRegisters(self):
        IO.output(self.rclk_Pin,0)
        for i in range(self.numOfRegisterPins-1,-1,-1):
            IO.output(self.srclk_Pin,0)
            val = self.registers[i]
            IO.output(self.ser_Pin,val)
            IO.output(self.srclk_Pin,1)
        IO.output(self.rclk_Pin,1)

    def clearRegisters(self):
        for i in range(0,self.numOfRegisterPins):
            self.registers[i] = 0
        self.writeRegisters()

    def allDots(self, OnOff):
        oldFlipDelay = self.flipDelay
        #self.flipDelay = .01
        if(OnOff):
            for column in range(self.displayColumns):
                for row in range(self.displayRows):
                    self.registers[self.onColumns[column]]=1
                    self.registers[self.onRows[row]]=1
                    self.oldDisplayState[column][row]=1
                self.writeRegisters()
                sleep(self.flipDelay)
                self.clearRegisters()
        else:
            for column in range(self.displayColumns):
                for row in range(self.displayRows):
                    self.registers[self.offColumns[column]]=1
                    self.registers[self.offRows[row]]=1
                    self.oldDisplayState[column][row]=0
                self.writeRegisters()
                sleep(self.flipDelay)
                self.clearRegisters()   
        self.flipDelay = oldFlipDelay       
    
    def simpleTest(self, rowDot, columnDot):

        self.registers[self.onColumns[columnDot]]=1
        self.registers[self.onRows[rowDot]]=1
        self.writeRegisters()
        sleep(.2)
        self.clearRegisters()
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

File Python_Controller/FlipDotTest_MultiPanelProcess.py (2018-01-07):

import FlipDot_Controller_Class
from time import sleep
import multiprocessing
import logging
import os

logging.basicConfig(level=logging.DEBUG,
                    format='(%(processName)-10s) %(message)s',
                    )

#----Set up controller to understand PCB design and Microcontroller layout----#
onRows = [11,19,16,20,23,21,22]
offRows = [53,61,56,60,57,59,58] 
onColumns = [54,52,51,50,49,48,47,46,45,55,62,63,64,65,66,67,68,69,70,71,44,43,42,41,40,76,75,74,73,72]
offColumns = [10,12,13,14,15,8,1,2,3,9,18,17,24,31,30,29,28,27,26,25,4,5,6,7,0,36,37,38,39,32]
numOfRegisterPins = 10 * 8 
FlipDot_Panels = [0 for i in range(3)]

#----Panel #1----#
ser_Pin = 18
rclk_Pin = 23
srclk_Pin = 24
FlipDot_Panels[0] = FlipDot_Controller_Class.FlipDot_Controller_Class(1, onRows, offRows, onColumns, offColumns, numOfRegisterPins, ser_Pin, rclk_Pin, srclk_Pin) 
#----Panel #2----#
ser_Pin = 17
rclk_Pin = 27
srclk_Pin = 22
FlipDot_Panels[1] = FlipDot_Controller_Class.FlipDot_Controller_Class(1, onRows, offRows, onColumns, offColumns, numOfRegisterPins, ser_Pin, rclk_Pin, srclk_Pin) 
#----Panel #3----#
ser_Pin = 5
rclk_Pin = 6
srclk_Pin = 13
FlipDot_Panels[2] = FlipDot_Controller_Class.FlipDot_Controller_Class(1, onRows, offRows, onColumns, offColumns, numOfRegisterPins, ser_Pin, rclk_Pin, srclk_Pin) 

columns_offset = 0
columns_at_a_time = 0
columns_each_character = 6
message = ''

def multiPanel(scroll_text, character_offset, scroll_speed):
	global columns_offset
	global columns_at_a_time
	global columns_each_character
	global message 
	message = scroll_text

	#----Do Initial Clearing----#
	for FlipDot_Panel in FlipDot_Panels:
		FlipDot_Panel.flipDelay = scroll_speed
		FlipDot_Panel.allDots(1)
		FlipDot_Panel.allDots(0)

	#----Start Scroller---#
	columns_offset = 0
	columns_at_a_time = character_offset
	columns_each_character = 6
	try:
		print "Press Ctrl+C to Stop Test."
		while True:
			if __name__ == '__main__':
				message = scroll_text+" "+scroll_text
				columns_offset_total = columns_offset*columns_at_a_time
				panelnum=0
				procs=[]
				panelnums = multiprocessing.Array('i', range(3))
				p = multiprocessing.Process(target=flipScroller,args=(panelnums,))
				p.start()
				p.join(10)
				if columns_offset>=(len(scroll_text)*columns_each_character)/columns_at_a_time:
					columns_offset=1
				else:
					columns_offset=columns_offset+1
	except KeyboardInterrupt:
		for FlipDot_Panel in FlipDot_Panels:
			FlipDot_Panel.deInitialize
		logging.debug('cancelling %s', p.name)
		for p in procs:
			p.terminate()
		pass

def flipScroller(panelnums, message):
	for i in range(len(panelnums)):
		logging.debug('Starting Panel #:'+str(i))
		c=i*5
		nMessage = message[c:]
		columns_offset_total = columns_offset*columns_at_a_time
		FlipDot_Panels[i].updateDisplay(nMessage,columns_offset_total)
		logging.debug('Exiting Panel #:'+str(i))
	return

def onOffer(panelNumber):
	logging.debug('Starting Panel #:'+str(panelNumber))
	FlipDot_Panels[panelNumber].allDots(1)
	FlipDot_Panels[panelNumber].allDots(0)
	logging.debug('Exiting Panel #:'+str(panelNumber))
	return

if __name__ == '__main__':
	message = raw_input("Scroll Text? ")
	character_offset = int(raw_input("Character Offset? "))
	scroll_speed = float(raw_input("Speed? "))
		#----Do Initial Clearing----#
	for FlipDot_Panel in FlipDot_Panels:
		FlipDot_Panel.flipDelay = scroll_speed
		FlipDot_Panel.allDots(1)
		FlipDot_Panel.allDots(0)
	panelnums = multiprocessing.Array('i', range(3))
	for n in range(5):
		character_offset = character_offset+1
		message = message[character_offset:]
		p = multiprocessing.Process(target=flipScroller,args=(panelnums,message))
		p.start()
		p.join()
	#multiPanel(message, character_offset, scroll_speed)
	for FlipDot_Panel in FlipDot_Panels:
		FlipDot_Panel.deInitialize
		sleep(.01)

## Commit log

2017-12-09 Added board and schematic - as well as pin layout file.
    [FlipDot_Controller.brd, FlipDot_Controller.sch, Flipdot_PCB_Layout_Lum.xlsx]
2017-12-10 Updated File Structure.
    [FlipDot_Controller.brd, FlipDot_Controller.sch]
2017-12-10 Added Gerber-generated pictures of PCB layout.
2017-12-10 Added PCB Gerber Files
2017-12-10 Updated Drill Files
2017-12-10 Updated Gerber Png Files
2017-12-10 Updated Board Design for Graphics.
    [FlipDot_Controller.brd]
2017-12-10 Added csv layout.
    [FlipDot_PCB_Layout_Lum.csv]
2017-12-10 Updated layout CSV for real Socket pin numbers.
    [FlipDot_PCB_Layout_Lum.csv]
2017-12-27 Updated to RPi from wiringpi
2017-12-27 Updated from wiringpi to RPi.GPIO
2017-12-27 updating multipanel threading
2017-12-27 Fixing range error in update display.
    [FlipDot_Controller_Class.py]
2017-12-27 Fixing Thread looping.
2017-12-29 updating index range problem in controller class.
    [FlipDot_Controller_Class.py]
2017-12-31 updating secondary pin layout
2018-01-04 Updating FlipDot for new voltage and multipanel.
    [FlipDotTest_MultiPanel.py, FlipDot_Controller_Class.py]
2018-01-06 Updating all files for cleanpup of old pin layouts.
2020-09-28 updated tests - ran them - and checked the display... getting some flipping power issues - but assume it is becasue of the connection to the pad...
    [FlipDotTest_Time2.py]
